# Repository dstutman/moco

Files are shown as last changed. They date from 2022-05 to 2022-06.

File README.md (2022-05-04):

# MoCo

Moco is a closed-loop brushless-motor controller. It is meant to glom onto the back of a 2805 gimbal motor and provide precise torque, speed, and position control.

## Versioning
Versioning is in vArB format. Incrementing B indicates a new revision has been produced that does not change external interfaces (form factor, communications, etc...). Incrementing A indicates a new version that changes these external interfaces. Until version 1 no there are no stability guarauntees.

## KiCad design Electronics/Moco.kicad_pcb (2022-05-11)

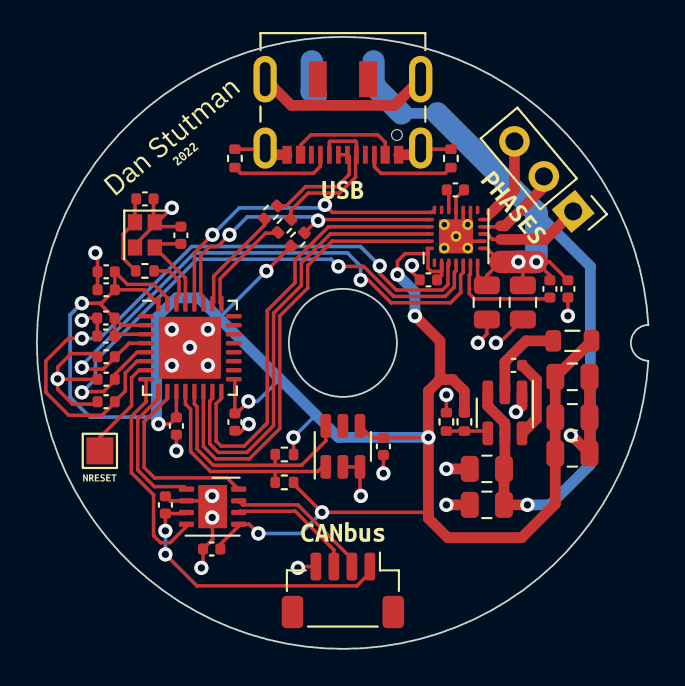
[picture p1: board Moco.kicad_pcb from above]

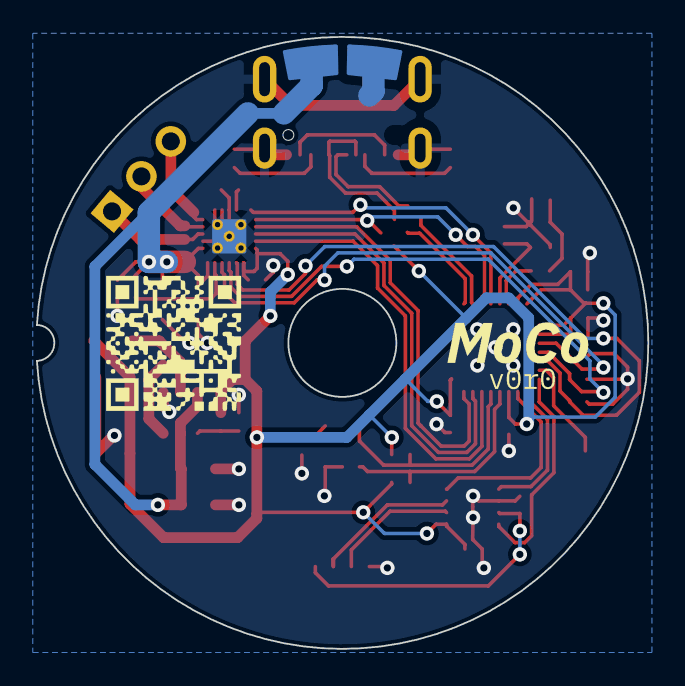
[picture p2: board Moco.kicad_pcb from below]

Board: 2 copper layers, 34.0 x 34.0 mm, 57 parts (4 on the bottom side), 37 nets.

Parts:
C1, C10: 1uF 6.3V; C_0402_1005Metric
C5: 0.1uF 10V; C_0402_1005Metric
C7: 0.1uF 6.3V X7R; C_0402_1005Metric
C8: 0.1uF 25V; C_0402_1005Metric
C9, C12, C14, C17, C21, C22, C23, C24, C25: 0.1uF 6.3V; C_0402_1005Metric
C11: 0.1uF VBUS; C_0402_1005Metric
C13, C15: 10uF VBUS; C_0805_2012Metric
C18: 10nF 6.3V; C_0402_1005Metric
C19, C20: XpF 6.3V; C_0402_1005Metric
C26, C27: 10uF 25V; C_0805_2012Metric
C28: 0.1uF; C_0402_1005Metric
C29, C30, C31: 22uF 6.3V; C_0805_2012Metric
J3: USB_C_Receptacle_USB2.0; USB_C_Receptacle_JAE_DX07S016JA1R1500
J4: Conn_01x03; PinHeader_1x03_P2.54mm_Vertical
J6: Conn_01x04; JST_SH_BM04B-SRSS-TB_1x04-1MP_P1.00mm_Vertical
J8, J9: Conn_01x01; Pad_CircularEdge_Ro16.5Ri15_Single
L2: 3.3uH 750mA; L_0805_2012Metric
R1, R2: 910R; R_0402_1005Metric
R4: 10 kR; R_0402_1005Metric
R5: 100R; R_0402_1005Metric
R6: 33.2kR; R_0402_1005Metric
R7: 10kR; R_0402_1005Metric
R8, R9: 5.1kR; R_0402_1005Metric
R10, R11: 22R; R_0402_1005Metric
TP1: TestPoint; TestPoint_Pad_1.5x1.5mm
U1: ESP32-C3; QFN-32-1EP_5x5mm_P0.5mm_EP3.45x3.45mm
U2: TPS562201; SOT-23-6
U3: TMAG5273; SOT-23-6
U4: DRV8311
U5: TJA1462ATK/0Z; HVSON-8-1EP_3x3mm_P0.65mm_EP1.6x2.4mm
Y1: 40 MHz +-10ppm; Crystal_SMD_2016-4Pin_2.0x1.6mm
kibuzzard-624C491C: G***; kibuzzard-624C491C
kibuzzard-626ED451: G***; kibuzzard-626ED451
kibuzzard-626ED465: G***; kibuzzard-626ED465
kibuzzard-626ED487: G***; kibuzzard-626ED487
kibuzzard-627B83F7: G***; kibuzzard-627B83F7
kibuzzard-6244CA09: G***; kibuzzard-6244CA09
kibuzzard-6244D452: G***; kibuzzard-6244D452
kibuzzard-62725C85: G***; kibuzzard-62725C85

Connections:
+3V3: C1.1, C7.2, C9.1, C12.1, C18.1, C21.1, C22.1, C23.1, C24.1, C29.2, C30.2, C31.2, L2.2, R1.2, R2.1, R4.1, R6.1, U1.2 (VDD3P3), U1.3 (VDD3P3), U1.11 (VDD3P3_RTC), U1.17 (VDD3P3_CPU), U1.31 (VDDA), U1.32 (VDDA), U3.4 (VCC), U4.2 (CSAREF), U4.24 (~SLEEP), U5.5 (VIO)
+5V: C5.1, J6.1, U5.3 (VCC)
/CANH: J6.2, U5.7 (CANH)
/CANL: J6.3, U5.6 (CANL)
/CAN_EN: U1.10 (MTDI/GPIO5/ADC2_CH0), U5.8 (STB)
/CAN_RX: U1.8 (GPIO3/ADC1_CH3), U5.4 (RXD)
/CAN_TX: U1.9 (MTMS/GPIO4/ADC1_CH4), U5.1 (TXD)
/DRV_~SCS: R4.2, U1.27 (U0RXD/GPIO20), U4.20 (~SCS)
/PWM_SYNC: U1.28 (U0TXD/GPIO21), U4.19 (PWM_SYNC)
/SCLK: U1.14 (GPIO8), U4.23 (SCLK)
/SDI: U1.15 (GPIO9/BOOT), U4.22 (SDI)
/SDO: U1.16 (GPIO10), U4.21 (SDO)
/SOA: C14.1, U1.4 (XTAL_32K_P/ADC1_CH0), U4.5 (SOA)
/SOB: C17.2, U1.5 (XTAL_32K_N/ADC1_CH1), U4.4 (SOB)
/SOC: C25.2, U1.6 (GPIO2/ADC1_CH2), U4.3 (SOC)
/TMS_SCL: R2.2, U1.12 (MTCK/GPIO6), U3.1 (SCL)
/TMS_SDA: R1.1, U1.13 (MTDO/GPIO7), U3.6 (SDA)
/USB_CONN_DN: J3.A7 (D-), J3.B7 (D-), R10.2
/USB_CONN_DP: J3.A6 (D+), J3.B6 (D+), R11.2
/USB_DN: R10.1, U1.25 (GPIO18/USB_D-)
/USB_DP: R11.1, U1.26 (GPIO19/USB_D+)
/~RESET: TP1.1, U1.7 (CHIP_EN)
GND: C1.2, C5.2, C7.1, C9.2, C10.2, C11.2, C12.2, C13.2, C14.2, C15.2, C17.1, C18.2, C19.2, C20.2, C21.2, C22.2, C23.2, C24.2, C25.1, C26.2, C27.2, C29.1, C30.1, C31.1, J3.A1 (GND), J3.A12 (GND), J3.B1 (GND), J3.B12 (GND), J3.S1 (SHIELD), J6.4, J9.1, R7.2, R8.1, R9.1, U1.33 (GND), U2.1 (GND), U3.2 (GND), U3.3 (TEST), U4.9 (PGND), U4.14 (AD1), U4.15 (AD0), U4.16 (AGND), U4.25 (PGND), U5.2 (GND), U5.9 (GND), Y1.2, Y1.4
unnamed: C8.2, U4.6 (CP)
unnamed: C10.1, U4.17 (AVDD)
unnamed: C19.1, U1.29 (XTAL_N), Y1.3
unnamed: C20.1, R5.1, Y1.1
unnamed: C28.1, L2.1, U2.2 (SW)
unnamed: C28.2, U2.6 (VBST)
unnamed: J3.A5 (CC1), R8.2
unnamed: J3.B5 (CC2), R9.2
unnamed: J4.1, U4.10 (OUTA)
unnamed: J4.2, U4.11 (OUTB)
unnamed: J4.3, U4.12 (OUTC)
unnamed: R5.2, U1.30 (XTAL_P)
unnamed: R6.2, R7.1, U2.4 (VFB)
Vdrive: C8.1, C11.1, C13.1, C15.1, C26.1, C27.1, J8.1, U2.3 (VIN), U2.5 (EN), U4.7 (VIN_AVDD), U4.8 (VM)

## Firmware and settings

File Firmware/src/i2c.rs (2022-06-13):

// TODO: Test and correct if issues
// Currently only designed for ESP32C3 with single I2C peripheral.
use core::sync::atomic::{AtomicBool, Ordering};

use esp32c3_hal::pac::{self, interrupt};

static INTERRUPT_TRIGGERED: AtomicBool = AtomicBool::new(false);

interrupt!(I2C_EXT0, i2c0_isr);
pub fn i2c0_isr() {
    INTERRUPT_TRIGGERED.store(true, Ordering::SeqCst);
}

#[derive(Debug)]
#[non_exhaustive]
pub enum Error {
    BusError,
}

pub enum BaudRate {
    Standard,
    Fast,
}

pub struct Master {
    regs: pac::I2C0,
}

impl Master {
    /// Creates a new `Master` control instance. Assumes desired pin
    /// configuration is already applied.
    pub fn new(regs: pac::I2C0) -> Self {
        // Enable the external crystal oscillator as the clock source
        regs.clk_conf
            .write(|w| w.sclk_sel().clear_bit().sclk_active().set_bit());
        // Configure the peripheral as a master
        regs.ctr.write(|w| w.ms_mode().set_bit());
        // Synchronize clock domains
        regs.ctr.modify(|_, w| unsafe { w.conf_upgate().set_bit() });
        Self { regs }
    }

    pub fn set_baudrate(&mut self, baud: BaudRate) {
        match baud {
            BaudRate::Standard => self.regs.clk_conf.modify(|_, w| unsafe {
                w.sclk_div_num()
                    .bits(100)
                    .sclk_div_b()
                    .bits(u8::MAX)
                    .sclk_div_a()
                    .bits(0)
            }),
            BaudRate::Fast => self.regs.clk_conf.modify(|_, w| unsafe {
                w.sclk_div_num()
                    .bits(40)
                    .sclk_div_b()
                    .bits(u8::MAX)
                    .sclk_div_a()
                    .bits(0)
            }),
        }
    }

    pub fn read(&mut self, device_id: u8, address: u8, data: &[u8]) -> Result<(), Error> {
        assert!(data.len() <= 32);
        // Transaction configuration
        // Command 0: START
        self.regs.comd[0].write(|w| unsafe { w.command().bits((0 << 11) | (1 << 8)) });
        // Command 1: WRITE
        // `data.len()` is u32, but high bits are guaranteed by
        self.regs.comd[1].write(|w| unsafe { w.command().bits((1 << 11) | (1 << 8) | 1) });
        // Command 2: RESTART
        self.regs.comd[2].write(|w| unsafe { w.command().bits((0 << 11) | (1 << 8)) });
        // Command 3: READ
        // `data.len()` is u32, but high bits are guaranteed unset by assert
        self.regs.comd[3]
            .write(|w| unsafe { w.command().bits((1 << 11) | (1 << 8) | data.len() as u16) });
        // Command 4: STOP
        self.regs.comd[4].write(|w| unsafe { w.command().bits((3 << 11) | (1 << 8)) });

        // Configure the slave address
        self.regs
            .slave_addr
            .write(|w| unsafe { w.slave_addr().bits(device_id as u16) });

        // Write data into the TX buffer in FIFO mode
        self.regs
            .data
            .write(|w| unsafe { w.fifo_rdata().bits(address) });

        // Synchronize clock domains
        self.regs
            .ctr
            .modify(|_, w| unsafe { w.conf_upgate().set_bit() });

        // Start the transaction
        self.regs.ctr.modify(|_, w| w.trans_start().set_bit());

        // Wait for transaction completion, then reset flag
        while !INTERRUPT_TRIGGERED
            .compare_exchange(true, false, Ordering::SeqCst, Ordering::SeqCst)
            .is_ok()
        {}
        let int_status = self.regs.int_status.read();
        // Reset the interrupt flags
        self.regs.int_clr.write(|w| unsafe { w.bits(u32::MAX) });

        // If we were triggered by a completed transaction, OK, else error
        if int_status.trans_complete_int_st().bit_is_set() {
            Ok(())
        } else {
            Err(Error::BusError)
        }
    }

    pub fn write(&mut self, device_id: u8, address: u8, data: &[u8]) -> Result<(), Error> {
        assert!(data.len() <= 32);
        // Transaction configuration
        // Command 0: START
        self.regs.comd[0].write(|w| unsafe { w.command().bits((0 << 11) | (1 << 8)) });
        // Command 1: WRITE
        // `data.len()` is u32, but high bits are guaranteed unset by assert
        self.regs.comd[1].write(|w| unsafe {
            w.command()
                .bits((1 << 11) | (1 << 8) | (data.len() + 1) as u16)
        });
        // Command 2: STOP
        self.regs.comd[2].write(|w| unsafe { w.command().bits((3 << 11) | (1 << 8)) });

        // Configure the slave address
        self.regs
            .slave_addr
            .write(|w| unsafe { w.slave_addr().bits(device_id as u16) });

        // Write data into the TX buffer in FIFO mode
        self.regs
            .data
            .write(|w| unsafe { w.fifo_rdata().bits(address) });
        for byte in data {
            self.regs
                .data
                .write(|w| unsafe { w.fifo_rdata().bits(*byte) })
        }

        // Synchronize clock domains
        self.regs
            .ctr
            .modify(|_, w| unsafe { w.conf_upgate().set_bit() });

        // Start the transaction
        self.regs.ctr.modify(|_, w| w.trans_start().set_bit());

        // Wait for transaction completion, then reset flag
        while !INTERRUPT_TRIGGERED
            .compare_exchange(true, false, Ordering::SeqCst, Ordering::SeqCst)
            .is_ok()
        {}
        let int_status = self.regs.int_status.read();
        // Reset the interrupt flags
        self.regs.int_clr.write(|w| unsafe { w.bits(u32::MAX) });

        // If we were triggered by a completed transaction, OK, else error
        if int_status.trans_complete_int_st().bit_is_set() {
            Ok(())
        } else {
            Err(Error::BusError)
        }
    }
}

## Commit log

2022-04-05 Add KiCAD outputs to gitignore
2022-04-05 Trade nFAULT for nSCS to avoid power on indeterminacy
    [Moco.kicad_pcb, Moco.kicad_sch]
2022-04-05 Update versioning scheme
    [Moco.kicad_pcb]
2022-04-25 Update silk (I think)
    I am not entirely sure what changes are in this commit. I think it is mostly
    just silk modifications.
    [Moco.kicad_pcb, Moco.kicad_sch]
2022-04-25 Switch from EFM32PG22 to EFR32BG22
    The EFM32PG22 is not currently available. The EFR32BG22 is downwards
    pin-for-pin compatible with it so I'll use that instead (for now).
    [Moco.kicad_pcb, Moco.kicad_sch]
2022-04-25 Update EFR32 part number
    [Moco.kicad_pcb, Moco.kicad_sch]
2022-04-25 Improve decoupling
    [Moco.kicad_pcb, Moco.kicad_sch]
2022-05-01 New design with ESP32-C3
    This design swaps the EFM32PG22 for an ESP32-C3. This reduces cost
    and improves availability. It also lets me use USB and CANbus instead
    of RS485.
    [Moco.kicad_pcb, Moco.kicad_sch]
2022-05-04 Complete ESP32-C3 redesign
    - Remove status LED to free up pin
    - Avoid using embedded flash SPI pins
    - Update silkscreen
    - Improve I2C and CANbus pin assignments
    [Moco.kicad_pcb, Moco.kicad_sch]
2022-05-11 Correct I2C net labels, add NRESET pad
    [Moco.kicad_pcb, Moco.kicad_sch]
2022-06-13 Add I2C driver
    Unverified, probably doesn't work yet
    [i2c.rs]
